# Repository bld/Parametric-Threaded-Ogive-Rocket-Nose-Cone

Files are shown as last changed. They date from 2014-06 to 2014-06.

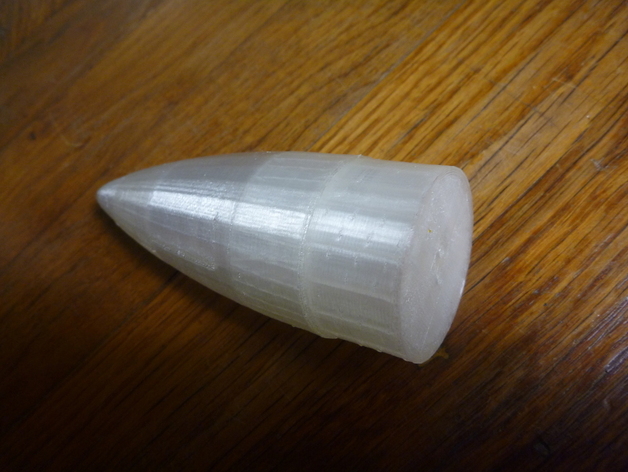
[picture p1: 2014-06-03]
img/Nosecone_and_base.jpg

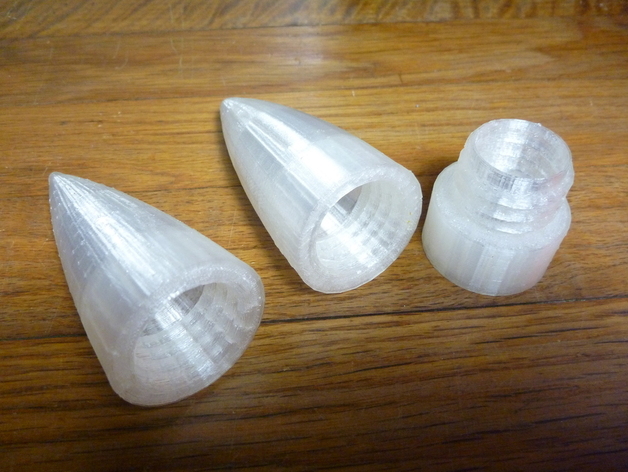
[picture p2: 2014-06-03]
img/Two_nosecones_with_base.jpg

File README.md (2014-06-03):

Parametric Threaded Ogive Rocket Nose Cone
==========================================

Fully parametric ogive nose cone with a screw-on base. This allows the
nosecone to be entirely printed, and used as a small payload bay. The
ogive shape is created by revolving a circular arc, combined with a
spherical tip. Uses syvwlch's thread library. More parametric model
rocket parts to come. Default size is for some extra thin-walled
1.63"/41.5mm diameter cardboard body tube I have. Includes integrated
reinforcement bar and mounting holes for tying a shock cord to the
base.

Licensed under [CC BY-SA 3.0](http://creativecommons.org/licenses/by-sa/3.0/).

Uses [Screw Library by syvwlch](http://www.thingiverse.com/thing:8793).

Instructions
------------

1. Download syvwlch's Screw Library: http://thingiverse.com/thing:8793
2. Measure body tube inner & outer diameters and enter
3. Select other parameters
4. Render & export STL for "fitcheck" part
5. Print fitcheck.stl and check fit in body tube. It shouldn't be too tight or too loose. You want it to come loose easily with the ejection charge, but not rattle around.
6. Adjust & reprint if necessary.
7. Print nosecone and base once the fitcheck part works to your liking.
8. Thread shock cord through holes in base and tie.
9. Screw cone onto base.

I printed this on my Makergear Mosaic with the following Slic3r settings:
* No support material
* 0.25 mm layer thickness
* 3 solid layers, 2 perimeters
* 0.1 fill density with rectilinear fill

Notes:
* The threads tend to curl up a little while printing at 0.25 mm, but the base and cone do so equally so the threaded together without trouble.
* Due to some slack in the threads, the base can end up slightly off-center when tightened. Unscrew and rescrew pressing away from the side that's short.
* Mine came out a little heavy, so for smaller, lighter rockets, check the balance to make sure it isn't too nose heavy: http://wikihow.com/Calculate-Stability-of-a-Model-Rocket

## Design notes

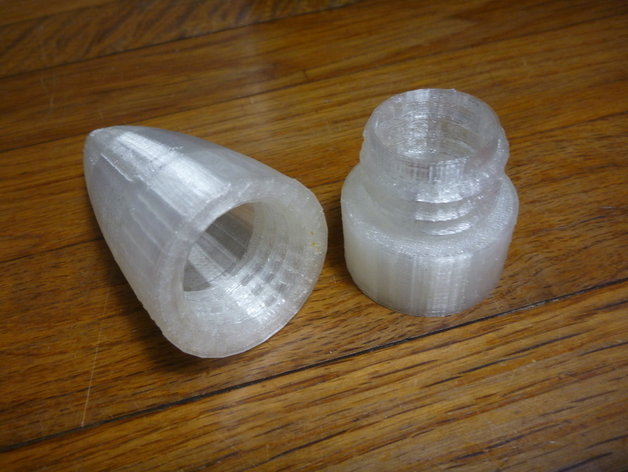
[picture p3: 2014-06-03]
img/Nosecone_and_base_apart.jpg

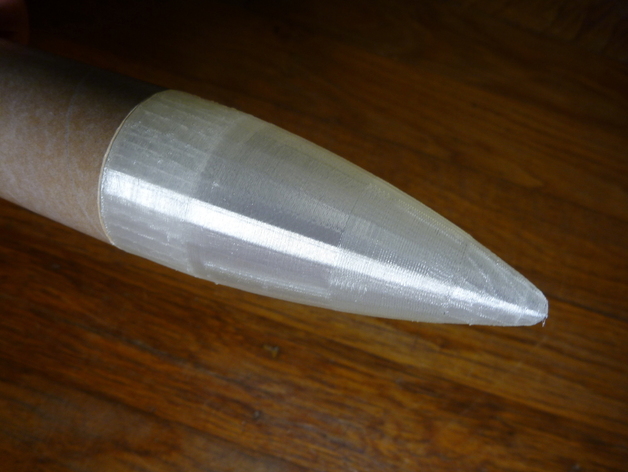
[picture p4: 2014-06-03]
img/Nosecone_in_tube.jpg

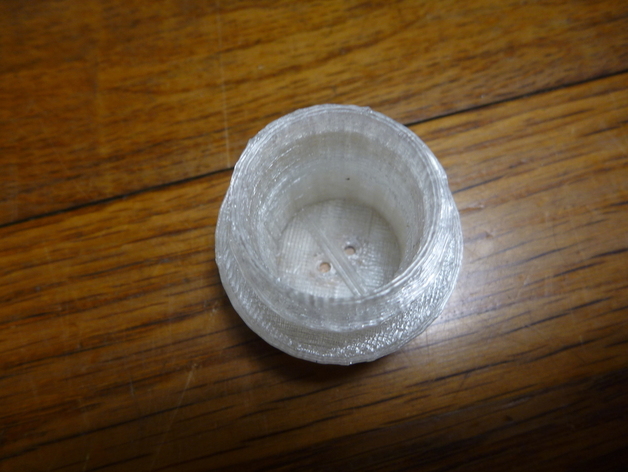
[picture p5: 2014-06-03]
img/Base_showing_shock_cord_attachment.jpg

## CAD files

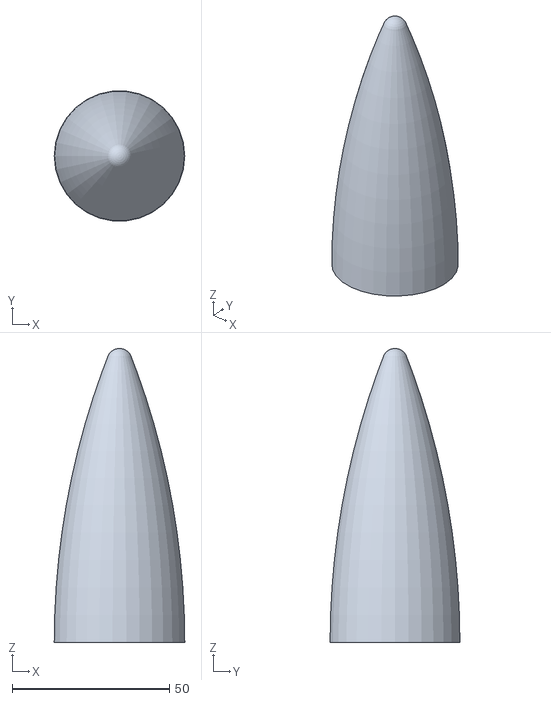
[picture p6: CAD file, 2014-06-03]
stl/ogive-threaded-cone.stl
41.5 x 41.3 x 93.5

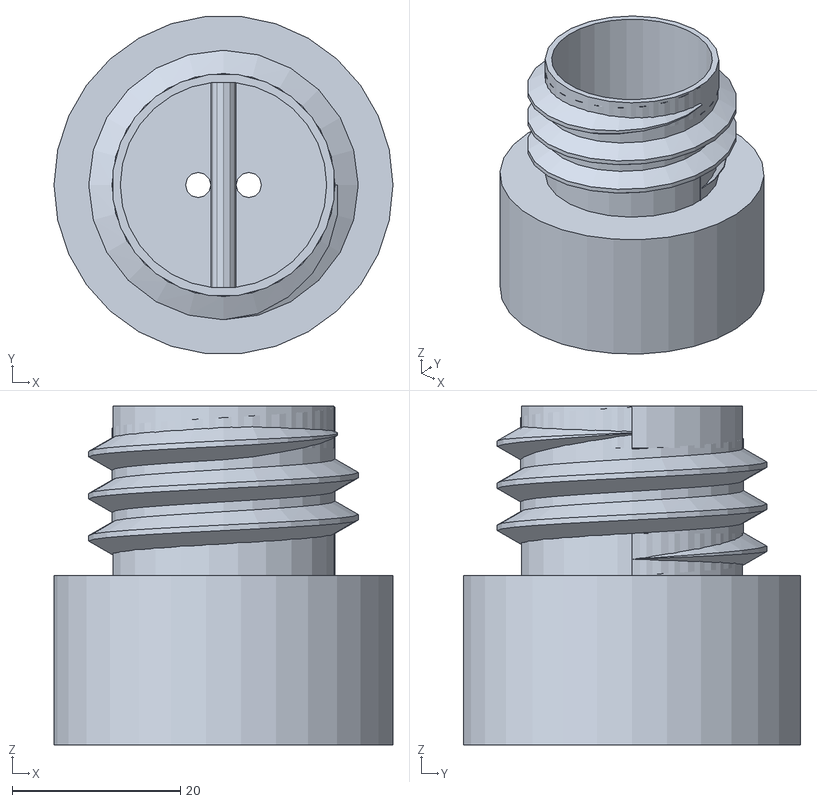
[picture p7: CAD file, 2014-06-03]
stl/ogive-threaded-base.stl
40.2 x 40.0 x 40.2

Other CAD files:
src/ogive-threaded.scad

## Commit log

2014-06-03 Updated README, added files & pictures
    [ogive-threaded-base.stl, ogive-threaded-cone.stl, ogive-threaded.scad]
2014-06-03 Changed location for githubiverse
    [ogive-threaded-base.stl, ogive-threaded-cone.stl, ogive-threaded.scad]
2014-06-03 Removed moved files
    [ogive-threaded-base.stl, ogive-threaded-cone.stl, ogive-threaded.scad]
